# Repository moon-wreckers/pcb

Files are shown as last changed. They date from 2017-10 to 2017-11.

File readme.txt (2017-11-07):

					Team I - MRSD'18
				Power Distribution Board
					   6 Nov 2017

Summary:
	
	The necessary features for the power distribtion board are to power the camera (12V, 0.42A), motor drivers 2x(12V, 15-20A), steering motors 2x(12V, 0.42A), the HTC VIVE beacon (12V, 0.40A), winch mechanism(5V, 0.90A), on-board computer(5V, 3A), GPS(5V, 0.08A) and inertial measurement unit (5V, 0.05A).
	
Maximum 12v Current: 42.06A
Maximum Theoretical Current: 45.19A
Total Nominal Current: 4.09A

Discussion:
	The on-board power supply is from a set of 12V batteries. Considering that majority of the on-board components have to powered using 12V supply - we have designed a 12V power distribution board, that further reduces to 5V wherever necessary. In order to have a bank of the 5V power supply pins, we have an off the shelf 12V-5V power regulator, that has been supplied with the on-board computer, as the power source to the extendable 5V power bank. 

	Further, in order to limit the power (current) drawn by various components the supply has been branched to shield components that have current limit less than or equal to 3A, 6.25A and 25A (15 + 6.25 +3 A).
	
	For example, the 12V to 5V regulator will be powered by the [12V, 3A] branch. Thus, protecting the components from (sudden, uncpredicted) excessive power requirements owing to unknown external conditions.

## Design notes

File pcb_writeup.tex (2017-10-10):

\documentclass[11pt]{article}
\usepackage[margin=20mm]{geometry}
\usepackage{amsmath}
\usepackage{listings,color,enumitem}
\definecolor{mygreen}{RGB}{28,172,0} % color values Red, Green, Blue
\definecolor{mylilas}{RGB}{170,55,241}
\usepackage{graphicx}
\title{Task 6\\ \vspace{2mm}\Large{16-681 MRSD Project Course }}
\author{
  Daniel Arnett \\
    Karthik (Venkata Rama) Paga\\
  Dicong (David) Qiu\\
  Matthew Swenson\\
  Abdul Zafar
}

\begin{document}
  \maketitle
    \newpage

\section{Regulator Efficiency} Linear voltage regulator efficiency is given by $1-\frac{V_{in}-V_{out}}{V_{in}}$.  So: 
$$\eta_{3.3V} = 1-\frac{24V-3.3V}{24V} = .1375$$
$$\eta_{5V} = 1-\frac{24V-5V}{24V} = .20833$$
$$\eta_{12V} = 1-\frac{24V-12V}{24V} = .5$$

\section{Input Power}

The input power for the motor at maximum rated output is 
$$
P_{\textit{IN},\textit{motor}} = \frac{\textit{\textit{motor}} \times I_{\textit{motor}, \textit{max}} }{\eta_{motor}} = \frac{24V \times 10A}{1.0} = 240W
$$

The input power for the CPU board at maximum rated output is 
$$
P_{\textit{IN},\textit{3.3V}} = \frac{\textit{\textit{3.3V}} \times I_{\textit{3.3V}} }{\eta_{3.3V}} = \frac{3.3V \times 1A}{0.1375} = 24W
$$

The input power for the Wifi and Encoder subsystem at maximum rated output is 
$$
P_{\textit{IN},\textit{5V}} = \frac{\textit{\textit{5V}} \times I_{\textit{5V}} }{\eta_{5V}} = \frac{5V \times 1A}{0.20833} = 24W
$$

The input power for the LIDAR at maximum rated output is 
$$
P_{\textit{IN},\textit{12V}} = \frac{\textit{\textit{12V}} \times I_{\textit{12V}} }{\eta_{12V}} = \frac{12V \times 2A}{0.5} = 48W
$$

\section{Total System Efficiency}

The total system efficiency at maximum rated output is 
$$
\begin{align*}
    \eta &= \frac{P_{\textit{motor}} + P_{3.3V} + P_{5V} + P_{12V}}{P_{\textit{IN}, \textit{motor}} + P_{\textit{IN}, 3.3V} + P_{\textit{IN}, 5V} + P_{\textit{IN}, 12V}} \\
    &= \frac{24V \timex 10A + 3.3V \times 1A + 5V \times 1A + 12V \times 2A}{240W + 24W + 24W + 48W} \\
    &= 0.8104
\end{align*}
$$

\end{document}

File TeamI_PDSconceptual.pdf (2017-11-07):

# Power Distribution System PCB

## Conceptual Design

Moon Wreckers, Team I
Abdul Moeed, David Qiu, Karthik Paga, Matt Swenson, Dan Arnett 2017 October 24

th

# Conceptual Design

## Power Supply

4 Batteries
3 Cells Each
11.1v Cells
Lithium Polymer
2650 mAh per Battery
Connected in Parallel

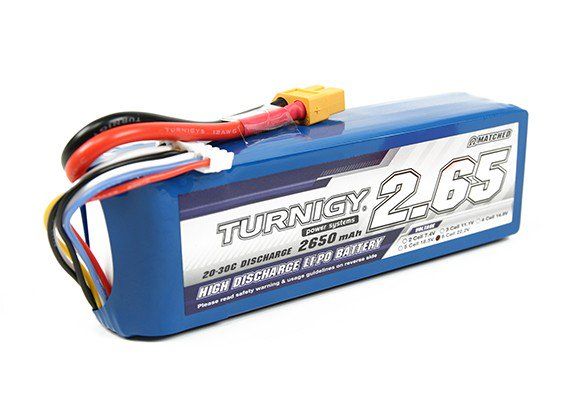
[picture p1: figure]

20-30C Discharge, meaning 20*2.65=53 to 79.5 Amps are available per battery
For our batteries we will use a standard XT-60 connector to prevent reverse voltage, and will use a digital display for test operators to view the rover’s operating voltage. We will not have an input switch.

## Power Requirements

Count | Voltage | Max Amperes | Name
1 | 12v | 0.42A | Camera GT1920C
2 | 12v | 0.40A | Lighthouse Beacon
2 | 12v | 20A (Stalled) | Drive Motors
2 | 12v | 0.42A | Steering Motors
1 | 5v | 3A | Odroid
1 | 5v | 0.08A | GPS
1 | 5v | 0.05A | IMU

Maximum 5v Current: 3.13a

Maximum 12v Current: 42.06A
Maximum Theoretical Current: 45.19A
Total Nominal Current: 4.09A
- For our motors and any other high current components we will use XT-60 connectors which are rated for 60 Amps.
- All connectors used will be non-reversible.
- 12v Connectors >= 7
- 5v Connectors >= 3
- We anticipate our voltage regulators to have roughly 90% efficiency, and our regulated 12v and 5v subsystems should have a nominal current draw of 0.9A and 1.8A respectively.
- We don’t plan on monitoring voltage or controlling power to any subsystems.
- Since our power source is 12v we will need to convert, regulate, and distribute 5v to three or more components.
- We will also regulate power to all of our 12v components except for our motors.

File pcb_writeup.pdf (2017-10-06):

## Task 6

## 16-681 MRSD Project Course

Daniel Arnett
Karthik (Venkata Rama) Paga Dicong (David) Qiu
Matthew Swenson
Abdul Zafar

October 6, 2017

1

## 1 Regulator Efficiency

Linear voltage regulator efficiency is given by 1 −

Vin−Vout
Vin

. So:

η3.3V = 1 −

24V − 3.3V
24V

= .1375

η5V = 1 −

24V − 5V
24V

= .20833

η12V = 1 −

24V − 12V
24V

= .5

## 2 Input Power

The input power for the motor at maximum rated output is

PIN,motor =

motor × Imotor,max

ηmotor

=

24V × 10A
1.0

= 240W

The input power for the CPU board at maximum rated output is

PIN,3.3V =

3.3V × I3.3V

η3.3V

=

3.3V × 1A
0.1375

= 24W

The input power for the Wifi and Encoder subsystem at maximum rated output is

PIN,5V =

5V × I5V

η5V

=

5V × 1A
0.20833

= 24W

The input power for the LIDAR at maximum rated output is

PIN,12V =

12V × I12V

η12V

=

12V × 2A
0.5

= 48W

## 3 Total System Efficiency

The total system efficiency at maximum rated output is

η =

Pmotor + P3.3V + P5V + P12V

PIN,motor + PIN,3.3V + PIN,5V + PIN,12V

=

24V 10A + 3.3V × 1A + 5V × 1A + 12V × 2A 240W + 24W + 24W + 48W
= 0.8104

2

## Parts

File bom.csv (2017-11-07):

Part | Value | Device | Package | Description | MANUFACTURER_PART_NUMBER | MF | MPN | OC_FARNELL | OC_NEWARK | VENDOR
3A_LINE | SE13 | SE13 | SE13 | SOLDER PAD E1542, drill 1,3mm, distributor Buerklin, 07F815
3A_LINE1 | SE13 | SE13 | SE13 | SOLDER PAD E1542, drill 1,3mm, distributor Buerklin, 07F815
6.25A_LINE | SE13 | SE13 | SE13 | SOLDER PAD E1542, drill 1,3mm, distributor Buerklin, 07F815
6.25A_LINE1 | SE13 | SE13 | SE13 | SOLDER PAD E1542, drill 1,3mm, distributor Buerklin, 07F815
25A_LINE | SE13 | SE13 | SE13 | SOLDER PAD E1542, drill 1,3mm, distributor Buerklin, 07F815
25A_LINE1 | SE13 | SE13 | SE13 | SOLDER PAD E1542, drill 1,3mm, distributor Buerklin, 07F815
C1 | 12000uF | C-USC1206K | C1206K | CAPACITOR, American symbol
C2 | 47uF | C-USC1206K | C1206K | CAPACITOR, American symbol
C3 | 47uF | C-USC1206K | C1206K | CAPACITOR, American symbol
CR1 | SMAJ5.0 | SMAJ5.0 | SMASERIES |  | SMAJ5.0 |  |  |  |  | Littelfuse Inc
CR2 | SMAJ5.0 | SMAJ5.0 | SMASERIES |  | SMAJ5.0 |  |  |  |  | Littelfuse Inc
CR3 | SMAJ5.0 | SMAJ5.0 | SMASERIES |  | SMAJ5.0 |  |  |  |  | Littelfuse Inc
D1 | BAT60J | BAT60J | SOD323_ST | Schottky barrier diode
D2 | BAT60J | BAT60J | SOD323_ST | Schottky barrier diode
D3 | BAT60J | BAT60J | SOD323_ST | Schottky barrier diode
F1 | 25A | TE5 | TE5 | FUSE |  |  |  | unknown | unknown
F2 | 6.25A | TE5 | TE5 | FUSE |  |  |  | unknown | unknown
F3 | 3A | TE5 | TE5 | FUSE |  |  |  | unknown | unknown
GND | SE13 | SE13 | SE13 | SOLDER PAD E1542, drill 1,3mm, distributor Buerklin, 07F815
GND2 | SE13 | SE13 | SE13 | SOLDER PAD E1542, drill 1,3mm, distributor Buerklin, 07F815
JP | 1 | PINHD-1X2 | 1X02 | PIN HEADER
JP@2 | 2 | PINHD-1X2 | 1X02 | PIN HEADER
LED1 | Green | LEDCHIPLED_1206 | CHIPLED_1206 | LED
LED2 | Red | LEDCHIPLED_1206 | CHIPLED_1206 | LED
LED3 | Yellow | LEDCHIPLED_1206 | CHIPLED_1206 | LED
LSP1 | SE13 | SE13 | SE13 | SOLDER PAD E1542, drill 1,3mm, distributor Buerklin, 07F815
LSP2 | SE13 | SE13 | SE13 | SOLDER PAD E1542, drill 1,3mm, distributor Buerklin, 07F815
LSP4 | SE13 | SE13 | SE13 | SOLDER PAD E1542, drill 1,3mm, distributor Buerklin, 07F815
LSP6 | SE13 | SE13 | SE13 | SOLDER PAD E1542, drill 1,3mm, distributor Buerklin, 07F815
LSP8 | SE13 | SE13 | SE13 | SOLDER PAD E1542, drill 1,3mm, distributor Buerklin, 07F815
PIN_BANK | 1 | PINHD-2X5 | 2X05 | PIN HEADER
PIN_BANK@2 | 2 | PINHD-2X5 | 2X05 | PIN HEADER
R1 | 1.2k | R-US_R1206 | R1206 | RESISTOR, American symbol
R2 | 150 | R-US_R1206 | R1206 | RESISTOR, American symbol
R3 | 560 | R-US_R1206 | R1206 | RESISTOR, American symbol
VIN_12V | SE13 | SE13 | SE13 | SOLDER PAD E1542, drill 1,3mm, distributor Buerklin, 07F815

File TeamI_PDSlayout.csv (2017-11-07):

Qty | Value | Part Designator | Description | Manufacturer/ Vendor Part Number | Vendor | Cost per part (USD)
1 | 1.2k | R1 | RESISTOR,American symbol | RC0402JR-071K2L | Digikey | 0.00139
1 | 12000uF | C1 | CAPACITOR,American symbol | SLPX123M063E9P3 | Digikey | 5.46
1 | 150 | R2 | RESISTOR,American symbol | ERJ-1GEF1500C | Digikey | 0.00671
1 | 25A | F1 | FUSE | 0678L9250-02 | Digikey | 0.3927
1 | 3A | F3 | FUSE | ERB-RE3R00V | Digikey | 0.114
2 | 47uF | C2,C3 | CAPACITOR,American symbol | CC0805MKX5R5BB476 | Digikey | 0.11257
1 | 560 | R3 | RESISTOR,American symbol | RC0402JR-07560RL | Digikey | 0.00139
1 | 6.25A | F2 | FUSE | 03136.25MXP | Digikey | 1.12
3 | BAT60J | D1,D2,D3 | Schottky barrier diode | SD0603S040S0R2 | Digikey | 0.08505
1 | Green | LED1 | LED | LTST-C191KGKT | Digikey | 0.29
1 | Red | LED2 | LED | LTST-C191KRKT | Digikey | 0.29
8 | SE13 | 3A_LINE,6.25A_LINE,25A_LINE,GND,LSP4,LSP6,LSP8,VIN_12V | SOLDER PAD E1542,drill 1,3mm,distributor Buerklin,07F815
3 | 5V | CR1,CR2,CR3 | Zener Diode | SMAJ5.0 | Littelfuse Inc | 0.51
1 | Yellow | LED3 | LED | LTST-C191KSKT | Digikey | 0.31
Parts that are not on board but necessary:
2 |  | UBEC-10A | Used as voltage regulators | UBEC 10A | Hobbying | 36.99

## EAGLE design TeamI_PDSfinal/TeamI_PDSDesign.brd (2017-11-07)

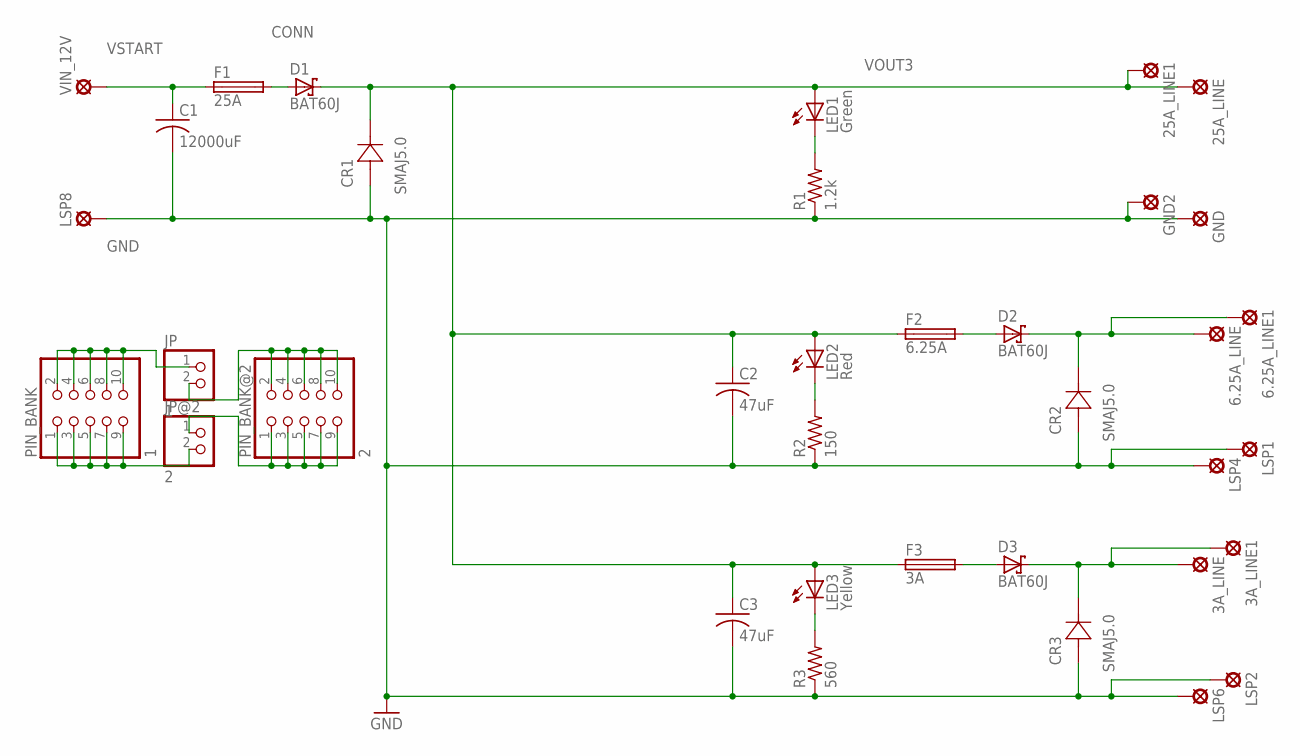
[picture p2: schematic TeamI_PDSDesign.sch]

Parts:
3A_LINE, 3A_LINE1, 6.25A_LINE, 6.25A_LINE1, 25A_LINE, 25A_LINE1: SE13
C1: 12000uF; C1206K
C2, C3: 47uF; C1206K
CR1, CR2, CR3: SMAJ5.0; SMASERIES
D1, D2, D3: BAT60J; SOD323_ST
F1: 25A; TE5
F2: 6.25A; TE5
F3: 3A; TE5
GND, GND2: SE13
JP: 1; 1X02
JP@2: 2; 1X02
LED1: Green; CHIPLED_1206
LED2: Red; CHIPLED_1206
LED3: Yellow; CHIPLED_1206
LSP1, LSP2, LSP4, LSP6, LSP8: SE13
PIN_BANK: 1; 2X05
PIN_BANK@2: 2; 2X05
R1: 1.2k; R1206
R2: 150; R1206
R3: 560; R1206
VIN_12V: SE13

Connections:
CONN: D1.A, F1.2
GND: C1.2, C2.2, C3.2, CR1.2 (1), CR2.2 (1), CR3.2 (1), GND.MP, GND2.MP, LSP1.MP, LSP2.MP, LSP4.MP, LSP6.MP, LSP8.MP, R1.1, R2.1, R3.1
unnamed: JP@2.1, PIN_BANK@2.1, PIN_BANK@2.3, PIN_BANK@2.5, PIN_BANK@2.7, PIN_BANK@2.9
unnamed: JP@2.2, PIN_BANK.1, PIN_BANK.3, PIN_BANK.5, PIN_BANK.7, PIN_BANK.9
unnamed: LED1.C, R1.2
unnamed: JP.1, PIN_BANK.2, PIN_BANK.4, PIN_BANK.6, PIN_BANK.8, PIN_BANK.10
unnamed: JP.2, PIN_BANK@2.2, PIN_BANK@2.4, PIN_BANK@2.6, PIN_BANK@2.8, PIN_BANK@2.10
unnamed: D2.A, F2.2
unnamed: 6.25A_LINE.MP, 6.25A_LINE1.MP, CR2.1 (2), D2.C
unnamed: LED2.C, R2.2
unnamed: D3.A, F3.2
unnamed: 3A_LINE.MP, 3A_LINE1.MP, CR3.1 (2), D3.C
unnamed: LED3.C, R3.2
VOUT3: 25A_LINE.MP, 25A_LINE1.MP, C2.1, C3.1, CR1.1 (2), D1.C, F2.1, F3.1, LED1.A, LED2.A, LED3.A
VSTART: C1.1, F1.1, VIN_12V.MP

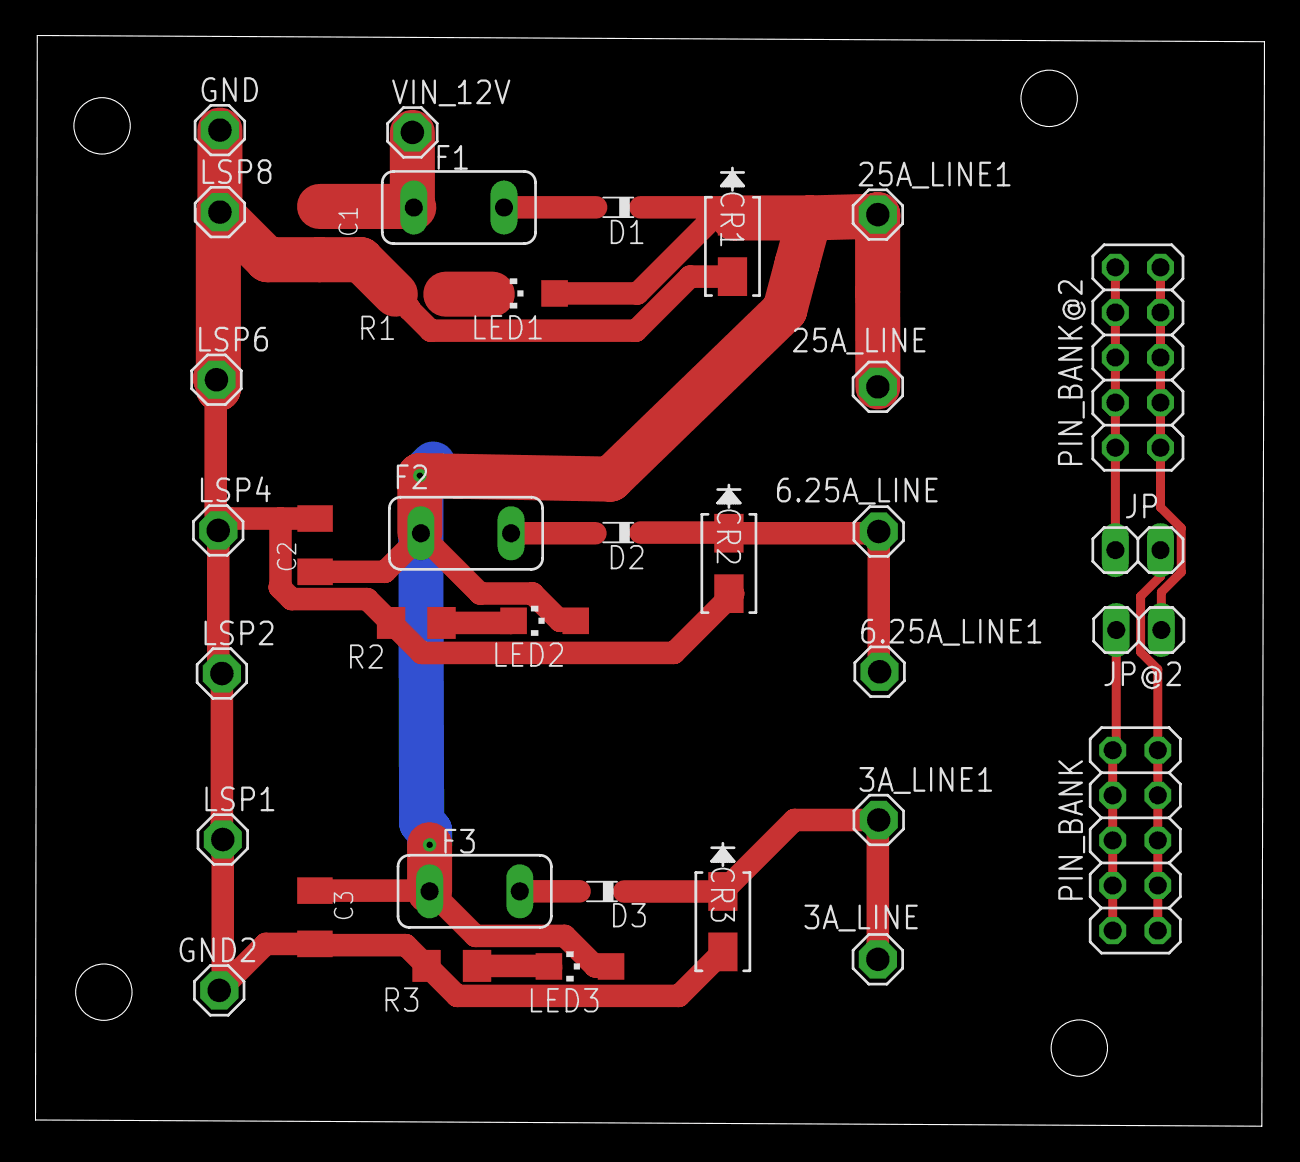
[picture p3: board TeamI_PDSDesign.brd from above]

Board: 2 copper layers, 69.2 x 61.4 mm, 36 parts (0 on the bottom side), 15 nets.

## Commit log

2017-10-05 added eagle libraries
    [Eagle\Eagle\Eagle.sch]
2017-10-05 vaguely rearranged board layout
    [Power Distribution Board Task 6.brd, Power Distribution Board Task 6.sch]
2017-10-06 update the schematic and layout
    [Power Distribution Board Task 6.brd, Power Distribution Board Task 6.sch]
2017-10-10 fixed stupid filenames
    [Eagle.sch]
2017-10-25 adding 12_5V_5A regulator
    [Eagle.sch]
2017-10-25 initial commit for swtiching the voltage regulators
2017-10-25 removed 3.3V regulation, corrected name tags, switched 5V regulator, removed terminal connectors (DAN will make surface mount pad in the layout)
    [Power Distribution Board Task 6.brd]
2017-10-25 changed stupid font size stupidly because eagle is stupid
    [Power Distribution Board Task 6.sch]
2017-11-02 found a DCDC converter
    [Eagle.sch]
2017-11-03 schematic with different current rating for 12V power supply
    [2ndNov_submission_12V_everywhere.brd, 2ndNov_submission_12V_everywhere.sch]
2017-11-03 finished board layout
    [2ndNov_submission_12V_everywhere.brd, 2ndNov_submission_12V_everywhere.csv]
2017-11-07 adding extenders for each 12V section
    [6thNov_submission_12V_everywhere.brd, 6thNov_submission_12V_everywhere.sch]
2017-11-07 ERC check complete
    [6thNov_submission_12V_everywhere.brd, 6thNov_submission_12V_everywhere.sch]
2017-11-07 moving BOM to git repo
    [TeamI_PDSlayout.csv]
2017-11-07 Gerber and BoM added.
    [2ndNov_submission_12V_everywhere.csv, 2ndNov_submission_12V_everywhere.sch, bom.csv]
2017-11-07 With Submission folder and Zip
    [TeamI_PDSBOM.csv, TeamI_PDSDesign.brd, TeamI_PDSDesign.sch]
